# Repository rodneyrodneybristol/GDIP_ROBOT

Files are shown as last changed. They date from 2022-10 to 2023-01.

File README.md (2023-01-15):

# UWE GDIP 2022, GROUP 7D RESISTOR SORTING ROBOT
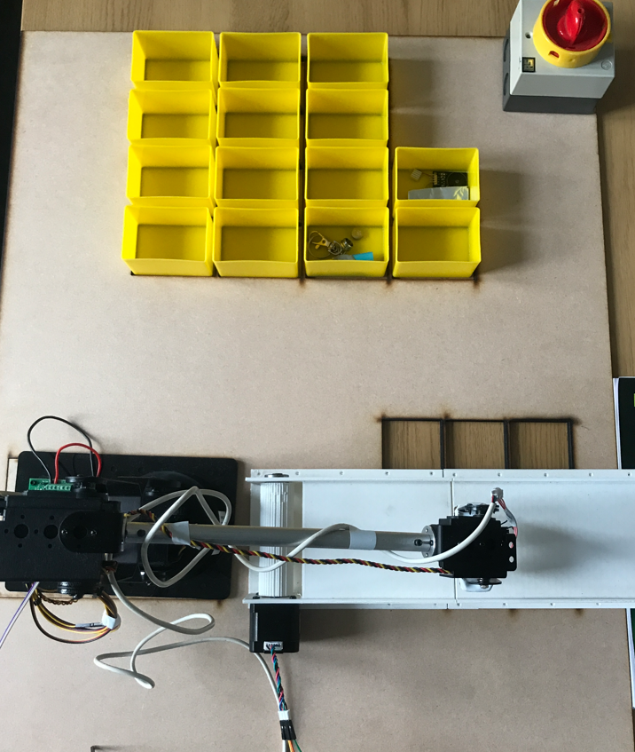
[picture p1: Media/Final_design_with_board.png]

<b>How to assemble and run</b>
<br>
To install:
<br>
```
git clone https://github.com/rodneyrodneybristol/GDIP_ROBOT
```
<br>
or download the .zip repository directly
<br><br>
Install platform IO, to open the firmware files for the motherboard and ohm meter board. 
<br>
Firmware may take a little while to load and build initially if you do not already have the Pi Pico SDK and Arduino frameworks installed. 
<br>
Firmware can be loaded to the Pi Pico directly and the Atmega328p can be programmed using an AVR programmer or Arduino in ISP programmer mode.
<br><br>
to 3D print the conveoyr belt, simply load the provided STLs in to any chopper software. Best to print them vertically to avoid excessive infil.
<br><br>
2 x 5V supplies, with at least 2A each are required  to run this system, one which handles the mobo/servos/ohm meter etc and another for powering the conveoyrs NEMA17 stepper motor. 
<br><br>
Calibration offset for the Robot can be adjusted in the 
```
startAndCalibrateArm();
``` function within the mobo/mainboard main.cpp file. These will need to be set once when loading the system, in case any servos have serious offsets. This allows for more precise movements of the arm.
<br><br>

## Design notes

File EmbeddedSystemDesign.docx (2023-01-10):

AL5D Robot arm project.

SHOULD WE MAKE THE CONTACT PLATE OURSELVES OUT OF COPPER?

# Problems to be solved

- Implement kinematic algorithm to move robot arm to location of resistor to be sorted.
- Read the value of a resistor using the 2 probes on the modified gripper design.
- Turn electromagnet on.
- Based on the returned value, tell the robot arm to sort the resistor into the appropriate container.
- Turn electromagnet off.
- Implement safety features (master stop).
- Implement Calibration features.
- Possibility of datalogging.

# Technical considerations.

Choice of embedded system.

First the documentation for the Lynxmotion ‘SSC-32u’ arm controller board was analysed. The control system uses a UART serial connection to receive control commands and to send some return data back as well. The UART connection could be configured to a desired baud rate and then controlled from any other device with a serial port.

A basic serial message to move all the servos on the robot arm can be sent in the form of a string, beginning with # and ending with a carriage return <cr>

#0P1425#1P1500#2P1500#3P700T2000<cr>

The first part of the command:

#0P1425

#0 means that servo 0 is being controlled, then p1425 sets that servo to that position. So 1P, 2P, 3P is then controlling another servo.

The last command:

T2000

Sets the travel speed in milliseconds, so in this example the motors will allow move to their desired positions in 2 seconds.

The absolute (maximum) control command was measured to be no greater than 34 Bytes, therefore that is the total length of a message in our system and memory allocation considerations going forward were based on that measurement.

To read the value of resistors, the gripper design is based on 2 probes which act like ohm meter probes to read the resistance of the gripper and an electro-magnet which then picks the resistor up for it to be sorted to a predefined location. For reliable measurements, the PCB to read the value must be mounted as close to the probes as possible, as noise and resistance could affect the analogue reading over longer distances.

Due to the reliability of serial communication over the working envelope of the robot arm:

(https://www.digikey.com/en/articles/uarts-ensure-reliable-long-haul-industrial-communications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,485%20or%20RS%2D422%20interfaces.)

“With appropriate line drivers, a UART can work over long distances: from 15 meters (m) for the RS-232 serial data bus to 1000 m for RS-485 or RS-422 interfaces” [22 May 2019]

The proposed design utilises an ohm meter on the arm itself, to read the value of the resistor and increase the reliability of that analogue reading, then send the processed reading to another “master” microcontroller which can then activate the robot arm. This will mean making 2 PCBs, one which could be mounted on the gripper and one to remain at the base acting as a master controller.

Given that the SSC-32u controller used serial messages to control the board, a serial connection would be needed for communication with the gripper and considering that the system may want to have flexibility to communicate with other devices such as a desktop computer alongside the arm controller. A microcontroller

Due to the recent upsets in the global semiconductor supply chain, certain, more popular microcontrollers, such as STM32F103vgt6 (core of the STM “blue pill”) and Atmega328p (core of the “Arduino Nano”) have become increasingly difficult to source, with back order waiting times sometimes over a year. An alternative solution was required here to bypass this issue.

Two contenders for the role in this case were the ESP32 or the RP2040 (Pi Pico/ Pico W). Seeking to keep the costs low and looking to develop further on a relatively new platform, the RP2040 was chosen due to its low cost and wide availability. The Pi Pico W development board was then set up to allow development of the system using breadboards, protoboard and in-house PCBs, made using a PCB router.

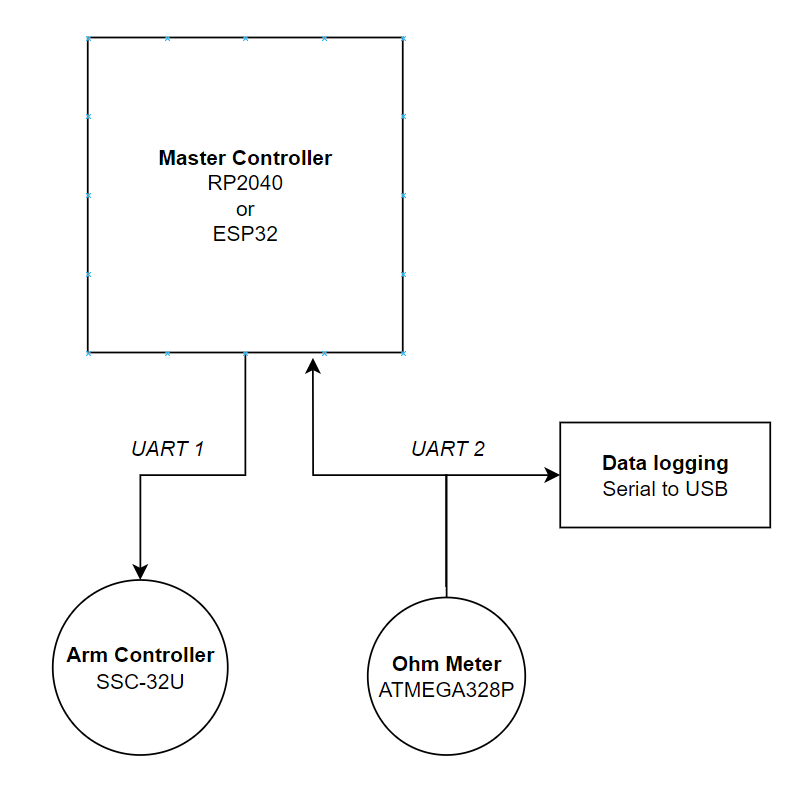
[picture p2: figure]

# Ohm Meter

The project required a system of reading values of resistance into a microprocessor, the value then denoting what box to sort the resistor in to.

Utilising an analogue to digital converter (ADC), resistance could be read from an unknown resistor by creating a voltage divider with that and another resistor of known value. Reading the voltage from that divider will give the resistance.

The resistance of known value is not random and does need to be within a relative range of that which is being tested. Thus, a feature which is seen in most multimeters, an auto ranging feature must be implemented to allow a wide range of values to be read without manually changing the resistor of known value.

The auto ranging design was chosen, using five PNP transistors, acting as switches between different known values of resistance, due to its small layout size compared to some other methods such as using an analogue multiplexer and some peripheral logic.

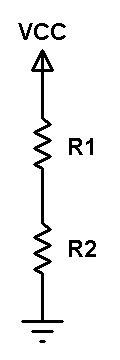
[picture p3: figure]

Applying voltage divider equation to the above circuit we get:
Voltage across resistor R1: VR1 = VCC x R1/(R1 + R2)
Voltage across resistor R2: VR2 = VCC x R2/(R1 + R2)

Assume that the resistance of R1 is known and R2 is unknown, by applying voltage divider equation we can easily get the value of R2 by measuring the voltage across it where: R2 = VR2 x R1/(VCC – VR2). If VR2 is equal to VCC then R2 = infinite.

How to measure R2 voltage (VR2):
The voltage is an analog signal and we can measure it using ADC (Analog-to-Digital) converter which converts analog data into digital data. The Arduino board with ATmega328P microcontroller (UNO, Nano, Mini …) has a built-in 10-bit ADC module where VCC (+5V) is represented by 1023 and 0 volts is represented by 0 (if VDD is already used as positive voltage reference).

Do we need fixed voltage reference?
Actually, I think there’s no need for a fixed voltage reference and adding it will not give a big change in the results. Because the voltage divider positive terminal (VCC) and the ADC positive reference voltage are connected to the same point and any change of this point voltage will affect both the voltage divider output and the ADC module.

Multirange ohmmeter:
To get a good value of the resistor to be measured, a multirange ohmmeter should be used.
The multi-range ohmmeter may also use voltage divider technique with different values of resistor R1. The following image shown a simple diagram of multi-range ohmmeter:

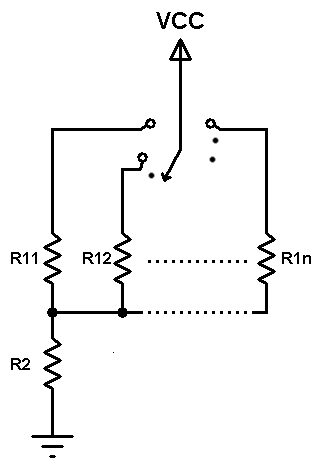
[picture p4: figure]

The multi-range ohmmeter is based on a mechanical switching device with 1 input and multi output. At any time just one known resistor (R11, R12 … R1n) is connected in series with the unknown resistor R2.

Auto-ranging ohmmeter:
The auto-range ohmmeter operates the same as the multi-range ohmmeter except that the mechanical switching device is replaced by electronic switches such as transistors driven by an intelligent device (microprocessor, microcontroller …) that decides which switch is closed according to the resistance value of the unknown resistor.

Project Hardware Required:

- Arduino board
- 5 x PNP transistor (2SA1015 (http://www.unisonic.com.tw/datasheet/2SA1015.pdf), 2N3906 (https://www.onsemi.com/pub/Collateral/2N3906-D.PDF) …)
- 2 x 100nF ceramic capacitor
- 5 x 4.7k ohm resistor
- 2M ohm resisor
- 100k ohm resistor
- 10k ohm resistor
- 1k ohm resistor
- 100 ohm resistor
- 330 ohm resistor
- 10k ohm variable resistor or potentiometer
- Breadboard
- Jumper wires

Arduino autoranging ohmmeter circuit:
Project circuit diagram is shown below.
Note that all the grounded terminals should be connected together.

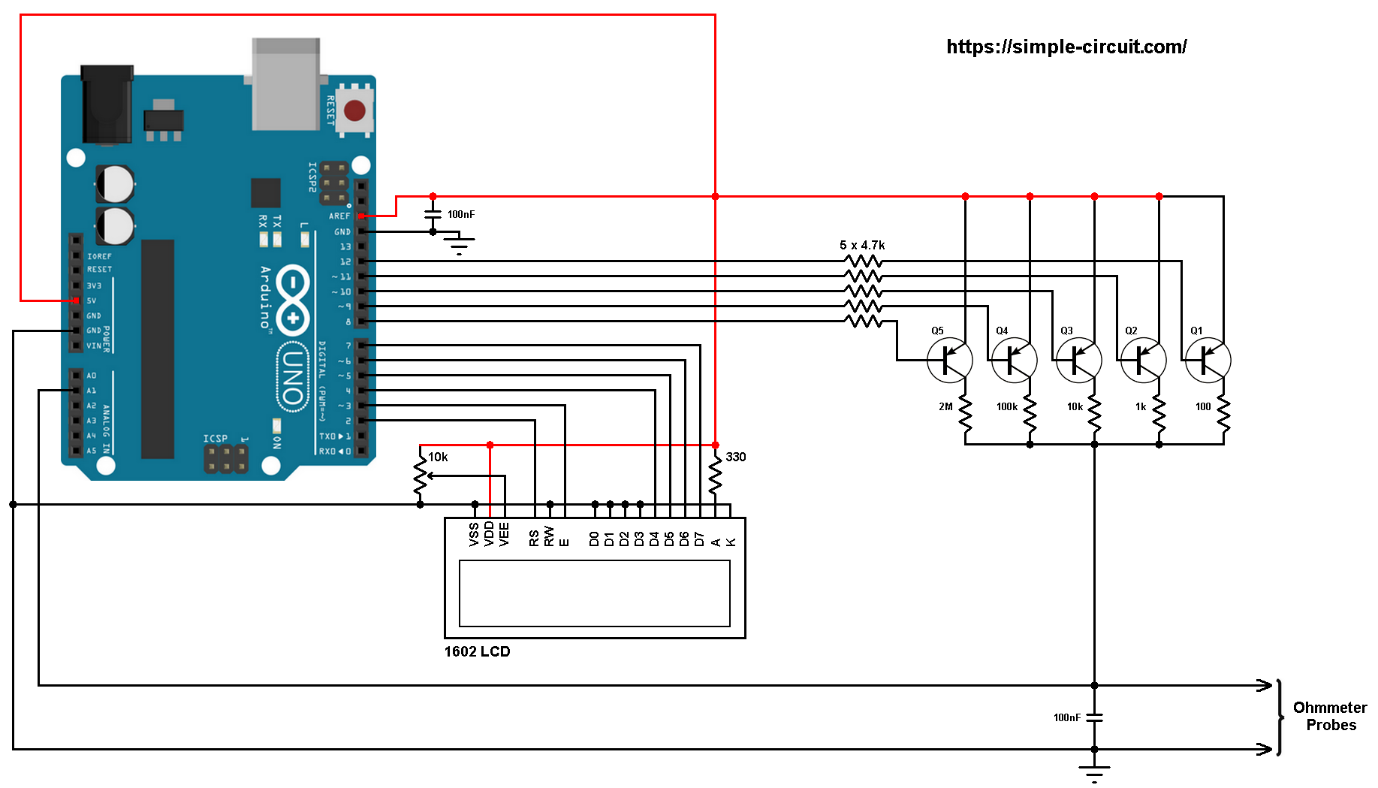
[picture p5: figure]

The resistor which we want to measure is connected between Arduino analog channel 1 (A1) and GND as shown in the above circuit diagram (Ohmmeter Probes). The 100nF capacitor is used to stabilize the voltage across the unknown resistor.

The five PNP transistors Q1 ~ Q5 are general purpose transistors and they are of the same type 2SA1015, 2N3906 or equivalent. They are used as electronic switches for our autoranging ohmmeter.
The emitter terminal of the five transistors are connected together to 5V pin of the Arduino board.

The collector of each transistor is connected to a different resistor. At any time there is only one ON transistor whereas the others are OFF. For better accuracy, each of the 5 resistors should have tolerance of 1% or lower.
Also, each transistor base is connected to Arduino digital pin through 4.7k ohm resistor.

The AREF pin of the Arduino board should be connected to 5V pin with 100nF capacitor between it and GND pin.

MY WORDS:

In the circuit diagram, the resistor being measured is connected between the A1 pin and GND on an Arduino board. A 100nF capacitor is included to steady the voltage across the unknown resistor. The circuit also includes five PNP transistors (Q1-Q5), which are all of the same type (2SA1015, 2N3906 or equivalent) and function as electronic switches for the ohmmeter. The emitters of the five transistors are all connected to the 5V pin on the Arduino board. Each transistor's collector is connected to a different resistor, with only one transistor turned on at a time. For improved accuracy, it is recommended that each of the five resistors has a tolerance of 1% or lower. The base of each transistor is connected to an Arduino digital pin via a 4.7k ohm resistor. Additionally, the AREF pin on the Arduino board should be connected to the 5V pin and have a 100nF capacitor between it and the GND pin.

# Master Controller

Since the master controller will require 2 separate UART connections, one for connecting to the ohm meter and another for connecting to the robot arm unit, using an ATMEGA328p based system would not be sufficient. Either an ESP32 (3 UART) or RP2040 (2 UART) based system would overcome this obstacle, both systems can be programmed using Arduino or Platform IO, as well as “bare metal” using their own respective SDKs.

# Electromagnet

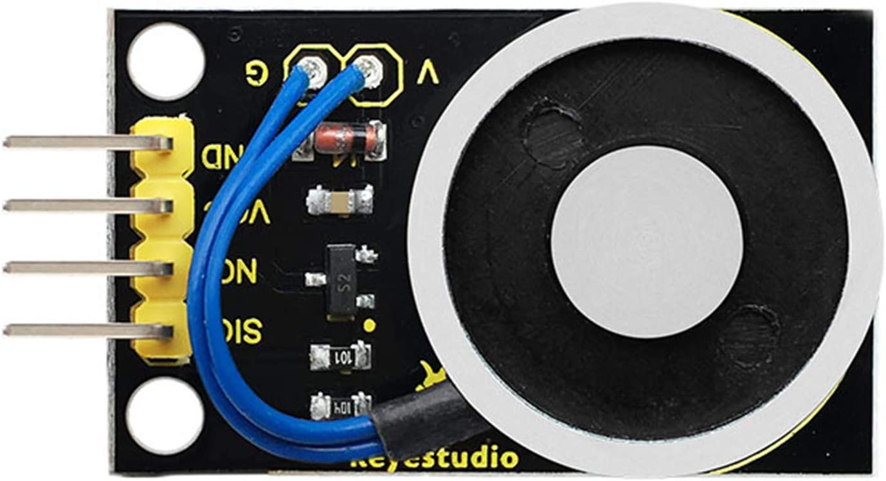
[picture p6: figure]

https://wiki.keyestudio.com/KS0320_Keyestudio_Electromagnet_Module_(Black_and_Environmental-friendly)

- Working Voltage: DC 5V
- Working current: 0.3A (maximum)
- Maximum power: 3W

The above electromagnet can be controlled using a PWM signal on its SIG pin, the larger the PWM value the larger the magnetic field (up to 1kg, this needs to be tested).

V & V

Managing bugs:

50% of microelectronics development is V&V as opposed to design. (lol wayyyy more)

Validation are we building the right system?

Verification ae we building the system right? (correctly?)

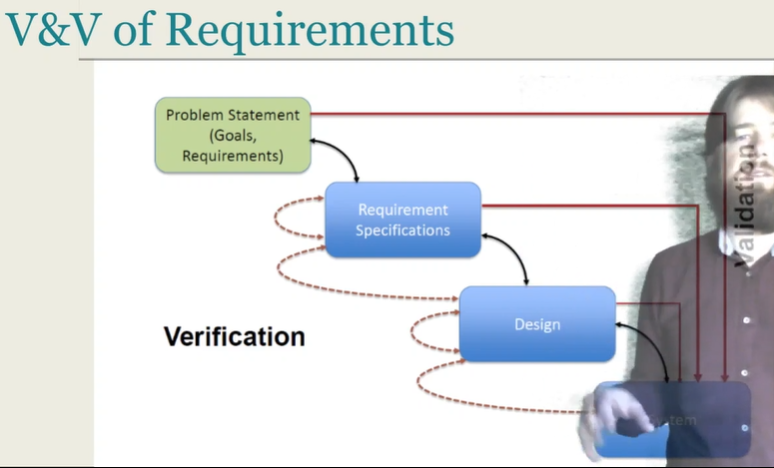
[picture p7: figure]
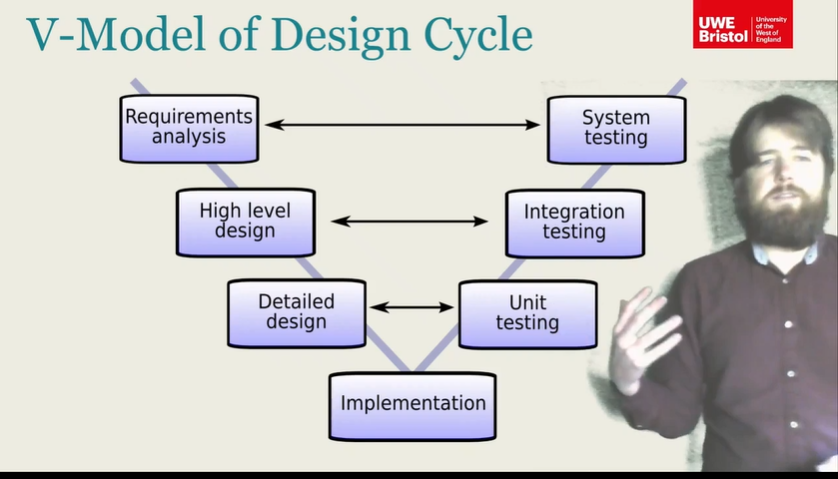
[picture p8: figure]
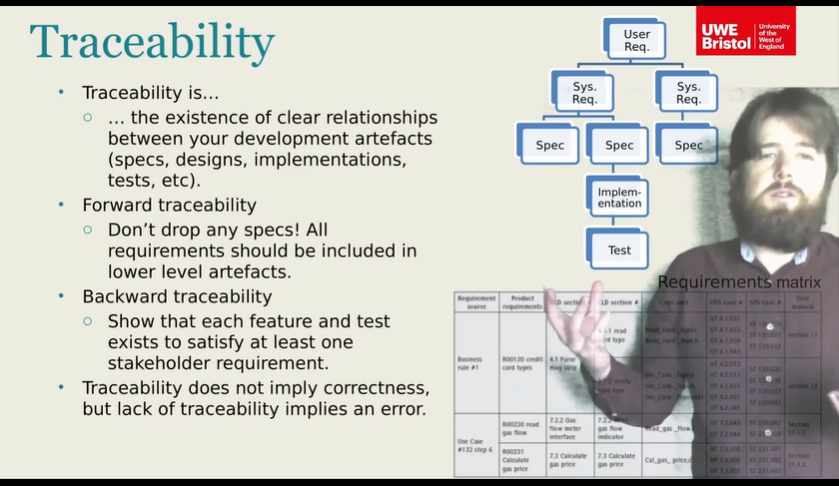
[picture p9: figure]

Requirements matrix

Talk about gripper iterations.

First one was too long, so mounted the PCB at 90 degrees to previous design.

Second design did not have correct mounting holes for the current al5d arm.

Third iteration did not have a solid enough infill and was very weak and broke on the first stress test. Potentially should add some sort of composite analysis here? This can be very basic.

Talk about initial building of system using Atmega328p on Arduino Nano, then upgrading the design to the raspberry pi pico, the pico and the RP2040 being much cheaper and readily available where as the Atmega328p is currently difficult to get hold of. Then finally settling on the Pico W with included WiFi capability to allow for possibility of exploring datalogging using JSON and an Amazon AWS server with get/puts.

Talk about the iterations of the base design and the justification for that in terms of allowing the system to be built by anyone using the cloned github repository.

Code snippets and pseudo code to justify the mathematical kinematic model.

Notes make 2nd gantt chart

PCB designs.

Take pictures of stuff

Summaries

What could we do better? Add datalogging and wifi control, better conveyor system. Have our own motor control board so as not to use the SCC-32u

Each row in this array is in the order, (x, y, resistance in ohms), and can be configured to any value between 100R to 2M

long BoxCoordinatesXY[10][3] = {

// Row 1

{0, 260, 1000}, //1k

{0, 330, 4700}, //4.7k

{0, 390, 10000}, //10k

// Row 2

{80, 270, 20000}, //20k

{80, 330, 47000}, //47k

{80, 390, 86000}, //86k

// Row 3

{160, 270, 100000}, //100k

{160, 330, 180000}, //180k

// Row 4

{240, 270, 470000}, //470k

{240, 330, 1000000}}; //1M

Calibration function

void startAndCalibrateArm()

{

Serial.println("#0P1425#1P1500#2P1500#3P700T2000\r"); // starting position

Serial.println("#2PO-100\r"); // calibrate

// DEBUG

delay(2000);

}

Kinematics string function
char *getArmCode(float x, float y, float z)

{

float grip_angle_d = 68;

// grip angle in radians for use in calculations

float grip_angle_r = radians(grip_angle_d);

// Adjustment so that the gripper hits the floor at z=0;

z += 70;

// Base angle and radial distance from x,y coordinates

// float d = sqrt( x*x + y*y ); //distance from base center to x,y coordinates

float phi = 90.00;

float bas_angle_r = atan2(x, y);

float L = sqrt((x * x) + (y * y));

// L is y coordinate for the arm

L -= cos(phi) * GRIPPER;

y = L;

// Grip offsets calculated based on grip angle

float grip_off_z = (sin(grip_angle_r)) * GRIPPER;

float grip_off_y = (cos(grip_angle_r)) * GRIPPER;

// Wrist position

float wrist_z = (z - grip_off_z) - BASE_HGT;

wrist_z -= sin(phi) * GRIPPER;

float wrist_y = y - grip_off_y;

// Shoulder to wrist distance ( AKA sw )

float s_w = (wrist_z * wrist_z) + (wrist_y * wrist_y);

float s_w_sqrt = sqrt(s_w);

// s_w angle to ground

// float a1 = atan2( wrist_y, wrist_z );

float a1 = atan2(wrist_z, wrist_y);

// s_w angle to SHOULDER

float a2 = acos(((sh_sq - el_sq) + s_w) / (2 * SHOULDER * s_w_sqrt));

// shoulder angle

float shl_angle_r = a1 + a2;

float shl_angle_d = degrees(shl_angle_r);

// elbow angle

float elb_angle_r = acos((sh_sq + el_sq - s_w) / (2 * SHOULDER * ELBOW));

float elb_angle_d = degrees(elb_angle_r);

float elb_angle_dn = -(180.0 - elb_angle_d);

// wrist angle

float wri_angle_d = (grip_angle_d - elb_angle_dn) - shl_angle_d;

// Servo pulses

float bas_servopulse = 1500.0 - ((degrees(bas_angle_r)) * 11.11);

float shl_servopulse = 1500.0 + ((shl_angle_d - 90.0) * 6.6);

float elb_servopulse = 1500.0 - ((elb_angle_d - 90.0) * 6.6);

float wri_servopulse = 1500 - (wri_angle_d * 11.1);

// Set servo pulses

// create string for output

// Added some offsets here, not sure if they are correct, they seem to work though

sprintf(output, "#0P%ld#1P%ld#2P%ld#3P%ldT2000\r", ftl(1500 - bas_servopulse + 500), ftl(shl_servopulse), ftl(elb_servopulse), ftl(wri_servopulse + 400));

return output;

}

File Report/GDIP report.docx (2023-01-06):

# Resistor sorting robotic arm

We could have an image of our arm here maybe?

Name | Student ID
Dominic Pennycook | 19006106
John Nicola | 19007312
Saad Khan | 20010279

Insert a table of figures after content – in the references tab under captions

Abbreviation | Meaning
RSA | Resistor Sorting Arm
V&V | Verification and Validation
MVP | Minimum Viable Product
V&V | Verification and Validation
RMP | Risk mitigation plan

# Introduction

## Purpose of the report

Due to the complex nature of the project and the high level of interest from stakeholders this report was created showing the process’s taken to ensure the products feasibility and suitability to the problem proposed and the project scope laid out later. Each section will aid in the completion of future project as well as show the suitable steps in an engineering projects lifecycle were completed to a high level. Important parts of the project management are included and the last key section of the report allows a deeper dive into what could be improved for future projects and what lessons were learnt.

## Scope of the project

The resistor sorting arm (RSA) needed to quickly and accurately sort through a group of resistors with minimal human assistance. The arm needed to measure resistor resistance in a set location, pick the resistor up and move it to the correct box. While our MVP works with the E12 resistor series modifications too the code would allow an easy change to a different set of resistors and with more altering additional boxed could be added allowing more different resistors too be sorted.

## All necessary documentation

GitHub was used extensively throughout the project allowing all pertinent documentation to be stored in one location. Use of software similar to GitHub allows excellent version control and advanced team collaboration and allowing individuals to produce documentation at their own rate. The link to this projects GitHub repository is XXX, and the can be found in the uploaded documentation on blackboard. The necessary password is XXX

# Project management

## Risks and Management

From the onset of the project risks were being assessed and added to the risk mitigation plan. Initially a comprehensive list of all related risks was created and then added to through the project, each team member regularly reviewed the plan and made sure it was still suitable. The risk was categorised using Figure XX & XX2, then using conditional formatting in excel it was it was simple to understand which risks were most dangerous to the project. Each of the initial risks were use in creating the Gantt chart and allowing additional time to events which had a higher likely hood of being delayed.

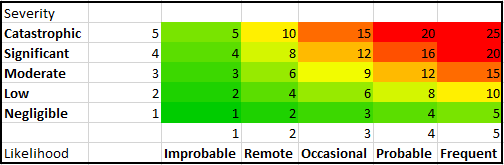
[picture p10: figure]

Figure 1 - Risk Characterisation Table

Figure 2 - Risk Key

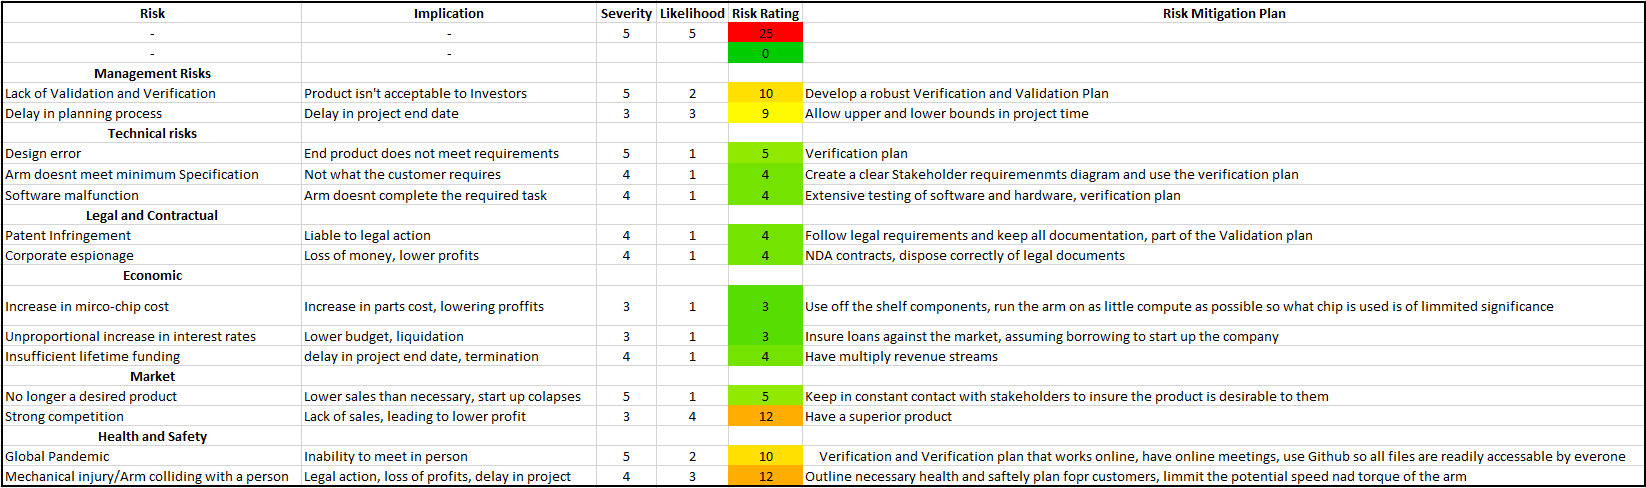
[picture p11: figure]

Figure 3 - Risk's and Mitigation Plans

The Verification and Validation (V&V) plan (covered later in this report) was vital to the success of the project. V&V allowed the confirmation that all sections accomplished were traceable to the system and high-level design, and also completed their intended outcome, without adding bloat to the project. As V&V was so vital to the project the robust plan was formed early on and rigidly maintained throughout the venture.

The Design risks heavily rely on a vigorous V&V plan, through this the likelihood of a project delaying/cancellation issue is extremely unlikely. This is further evidence of the need for a competent V&V plan. Legal and contractual issues would be a greater issue past this project’s scope and after the production of the minimum viable product (MVP) but designing the arm from scratch will minimise these issues. Economic issues are largely out of the control of the start-up, however suitable mitigation in the case of an issue is still needed and provided. Through continued discussion with the stakeholders, described in the High-level design section, there is an undersaturated market for this product and minimal competition. However, if the market decreased/becomes oversaturated this could financially cripple the company so continued talks are necessary. As with any product, a suitable look into health and safety in the manufacture and use of the product is necessary and the necessary documentation will be provided for both.

The RMP was regularly updated periodically in conjunction with the project and GitHub as used for version control ensuring all different stages of the plan were saved and could be accessed if needed. As the RMP was created originally at the beginning of the project all team members knew what the risks were and how to avoid them happening allowing the project to complete smoothly with minimal issues.

## Team allocation

At the start of any project, it is vital to determine and define the team structure and roles, making sure everyone in the team understands their responsibility and roles. This breakdown is detailed in Figure XX 4). To further emphasise each team members roles and responsibility a responsibility matrix was created (Figure XX 5). This level of planning allowed team members to know what they needed to complete and who had the information to help them, also allowing individual members to make sure everyone else had completed their section.

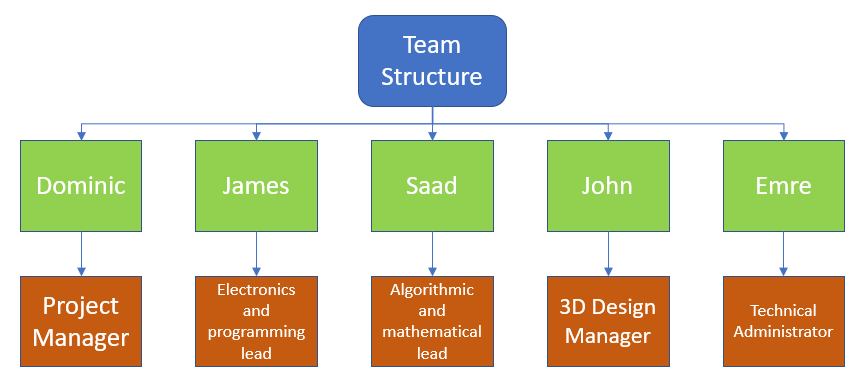
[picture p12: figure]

Figure 4 – Team structure

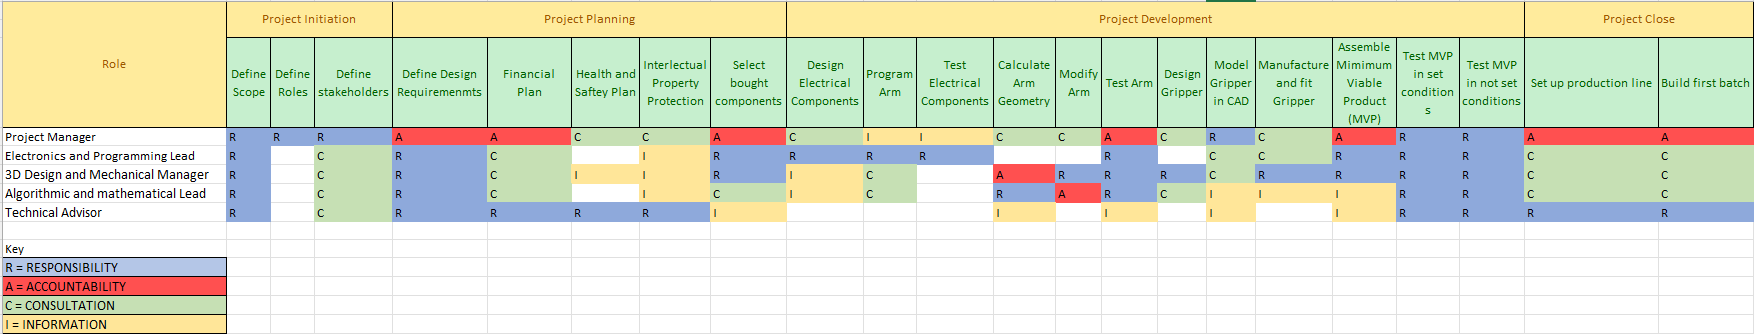
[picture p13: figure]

Figure 5 - Responsibility matrix

## Planning and Scheduling

- Planning and scheduling

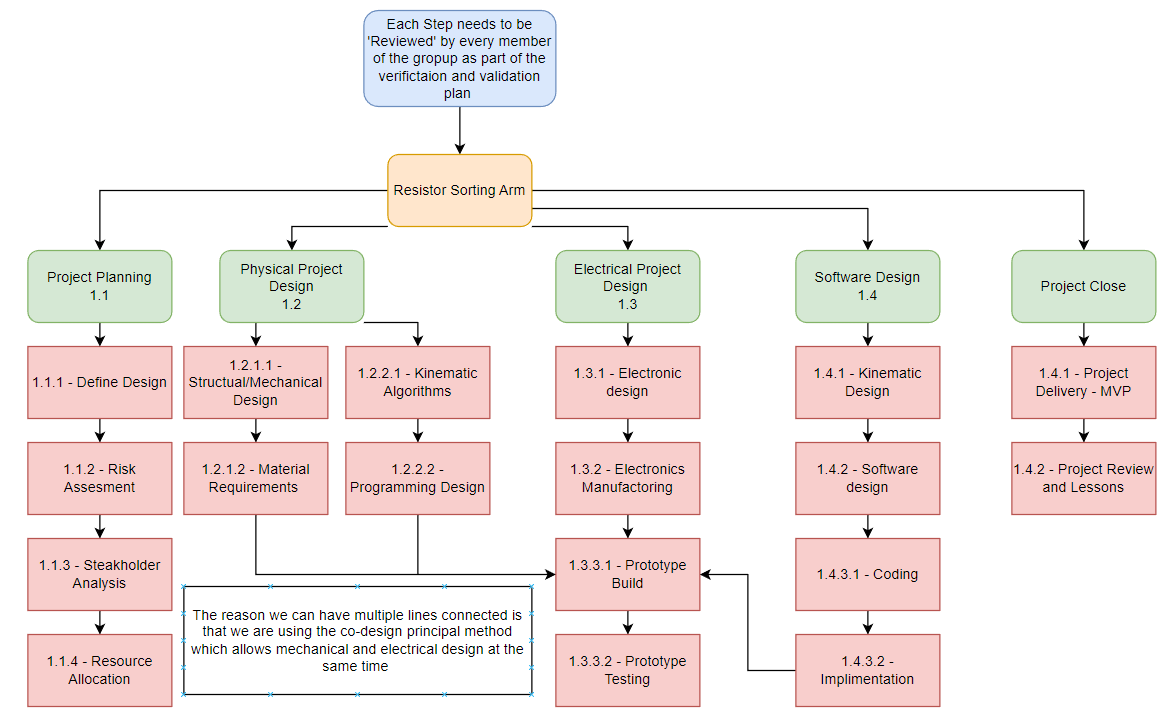
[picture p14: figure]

Figure 6 - Work Breakdown Structure

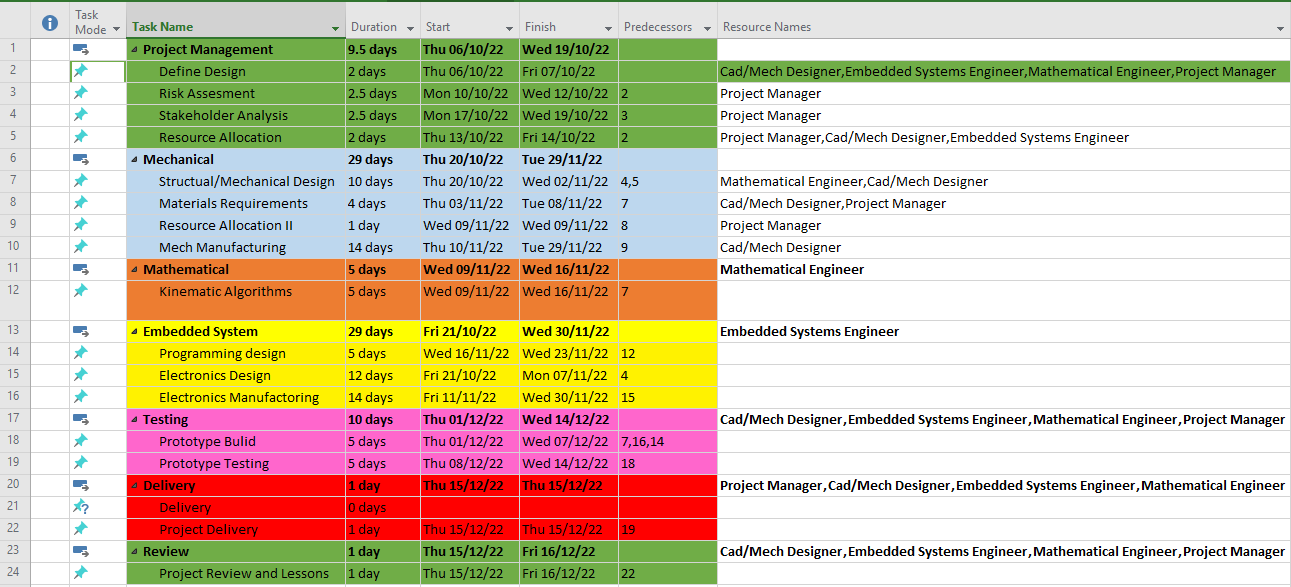
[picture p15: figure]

Figure 7 - Project Gant Chart 1

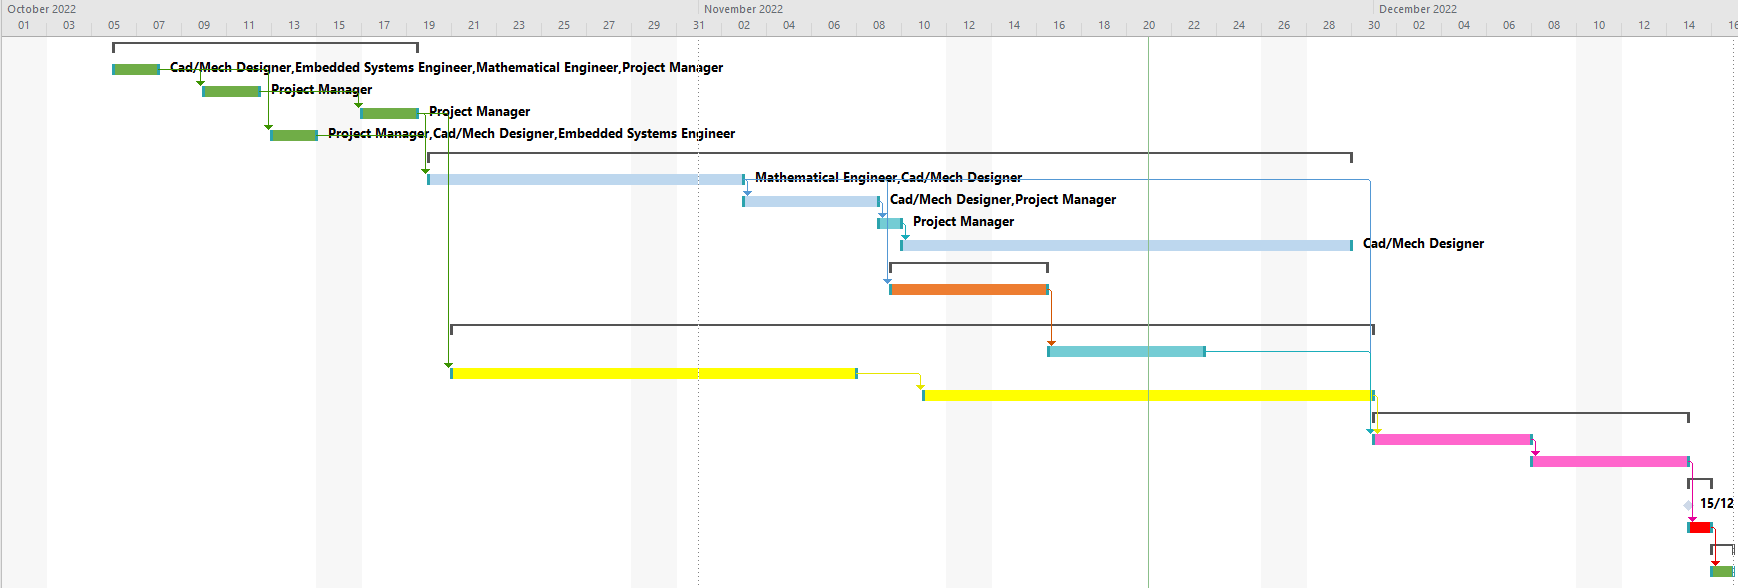
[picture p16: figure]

Figure 8 - Project Gant Chart 2

## Progress monitoring and Coordination

During the project weekly meetings were held and comprehensive meeting minutes were taken, as seen in the GitHub repository. This allowed everyone to know what had been discussed and also what they need to complete in order to stay on track and complete the project in time. Any task that was not completed for any reason was moved too the next weeks minutes and the project manager followed up with help to make sure they were completed. This use of meeting minutes on GitHub gave clear instructions to every team member on what was necessary to be completed, when uploaded to GitHub the meeting minutes document was available to everyone and any changed that were made would be visible.

# High-level design

## Top-Level System Design

- Presentation of top-level system design. Clear presentation of top-level system design. Clear presentation of high-level design of the main subsystems (e.g. software, electronics). High level designs address all requirements appropriately.

Top level system design and high-level design require conversation with the stakeholders, to ensure all stakeholders are considered each team member had a template stakeholder analysis which allowed multiple stakeholders and their importance along with other metrics which decided their allocation in the stakeholder management document. With each team member independently conceiving a stakeholder analysis the likelihood of a potential stakeholder being missed is drastically reduced allowing a more exhaustive management of the stakeholders. All members included the electronics technical help team at the University of the West of England as a key stakeholder providing the unique possibility to have their opinion every week during the meetings held. This close management of a key stakeholder allowed the project to stay on track and gave very good system and high level design criteria.

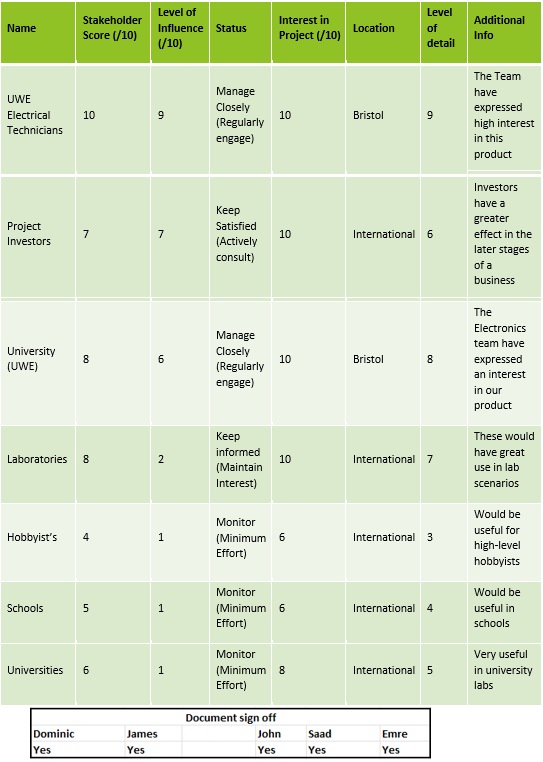
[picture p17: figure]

Figure 9 - Stakeholder Analysis

Utilising the stakeholder analysis and either talking directly to the stakeholder or using our tutor as that stakeholder a list of all the requirements (Figure XX) was created and the stakeholder sign off was used. This requirements list document allowed a clear view of what was desired by the clients and what we needed to do to complete the project to satisfaction. Once the stakeholders, the UWE Fet Team and a representative group of hobbyists, had read the requirements list any changes were made and the document was signed off.

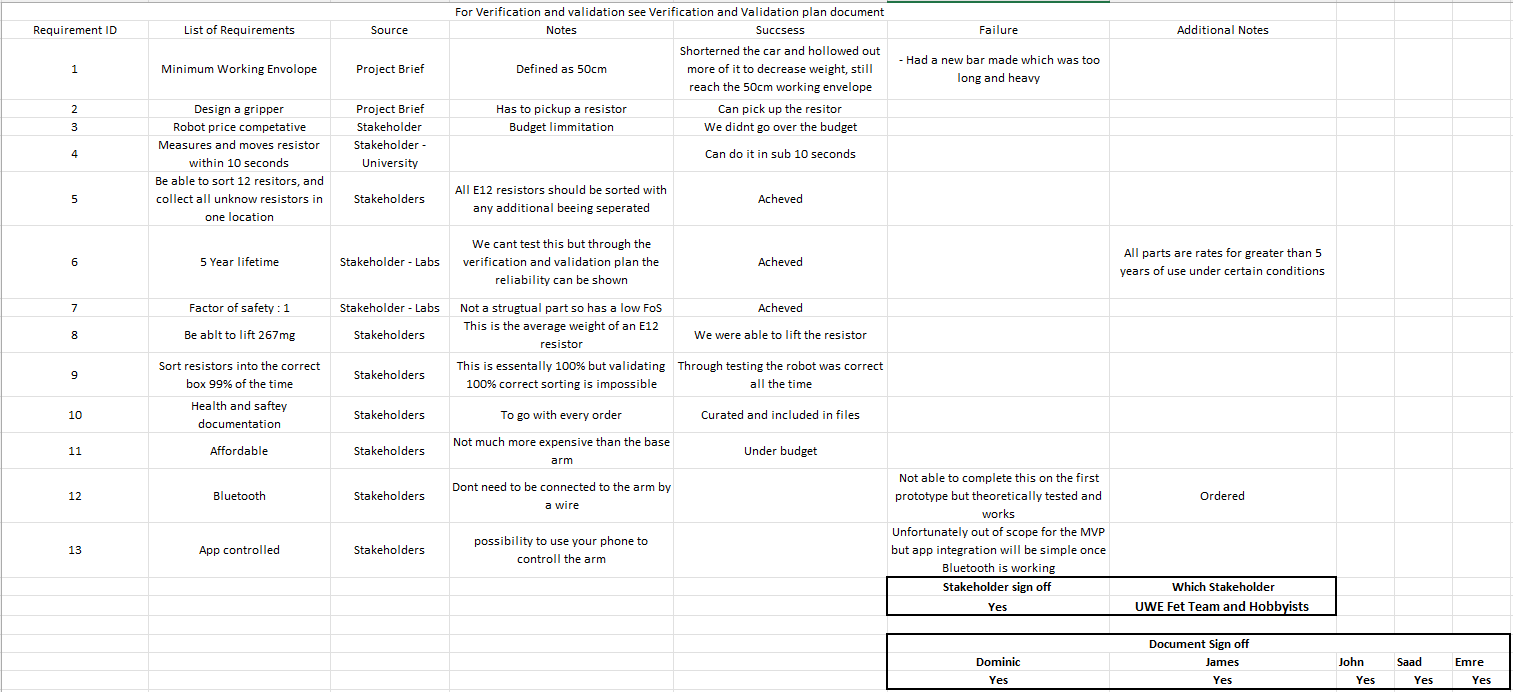
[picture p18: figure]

Figure 10 - Requirements list

## High-Level Mechanical Design

- Presentation of high-level design of the main subsystems (e.g. software, electronics).

## High-Level Software Design

- Presentation of high-level design of the main subsystems (e.g. software, electronics).

## High-Level Electrical Design

- Presentation of high-level design of the main subsystems (e.g. software, electronics).

## Requirement Analysis

'- Requirements analysis

## Traceability

The High Level design requirements were specified from user requirements, as is corroborated by the Requirements list. This list was form in collaboration with various stakeholders to produce a comprehensive idea of what the robot was required to complete. Each high-level design has a direct link to s system level design validating that the stakeholders would want it.

# Financial, Regulatory and Intellectual Property considerations

# Low-Level Design

## Implementation

'- Lower-level specifications and implementations to address the requirements.

- description of the process for developing and implementing the low-level designs, including justification of key decisions.

Things to include: create specifications that each design must fulfil, and mark against design

Justification of the base – why we created a base/ its purpose - mechanical

Why we created an electromagnetic gripper, process of coming to that conclusion, difficulties with a mechanical based gripper - mechanical

How the gripper works - electrical

Reason for having a treadmill/ something to put resistors on (idk what its actually called) - mechanical

How we measured the resistance/ why we did it this way? - electrical

Explanation of kinematics code – software

Maybe should also include some stuff on the programming?

Have a sequence diagram of how the outside world interacts with our robot and how it interacts with the world

- Will look into this

## Low-Level Documentation

- Clear and accessible documentation of low-level designs.

Gripper, base design, maybe some electromagnet stuff

## Traceability

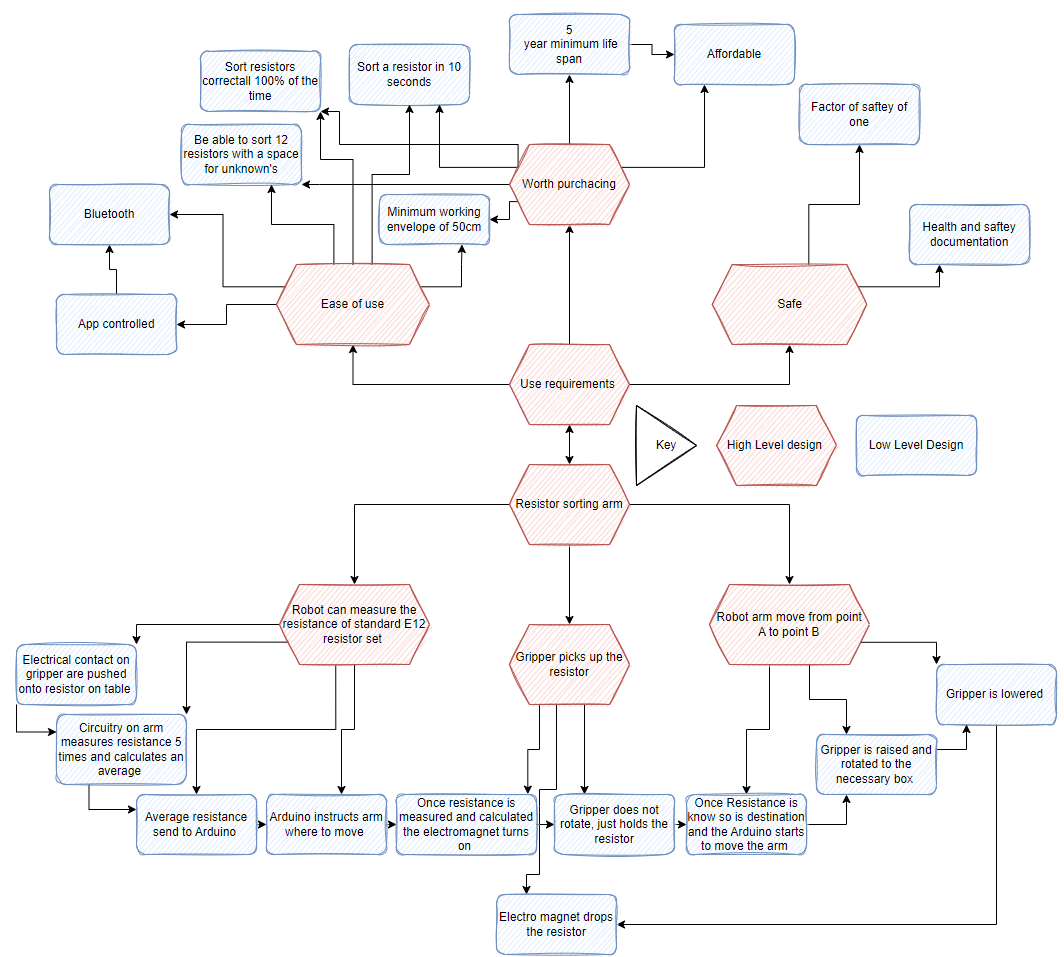
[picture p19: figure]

Figure 11 - High -> Low level design with traceability

# Verification and Validation (V&V)

## V&V Plan

The V&V plan ensures that the end product is designed and built well and what the customer desired. To accomplish this a competent V&V plan was created at the onset of the project and strictly adhered to, this relied heavily on the V&V matrix (Figure XX) and the individual sign off.

A V&V matrix (Figure XX) allows for every key aspect of the project to be officially tested and verified to both work, and contribute to what is desired by the stakeholders. Each of the high-level designs and the lead team member(s) are listed with the ID of the verification used and whether this provided full of partial coverage. The different verifications used are found on the next sheet (Figure XX) and these describe the actions taken and are referenced using ID tags for ease of use. The V&V plan was used throughout the project and shows how successful the project was.

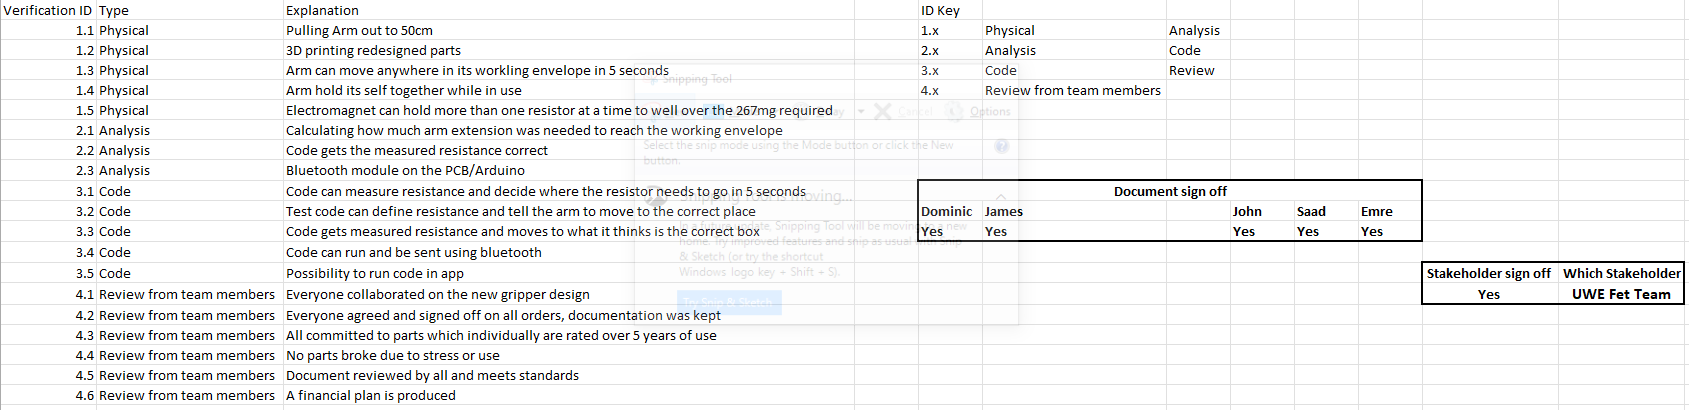
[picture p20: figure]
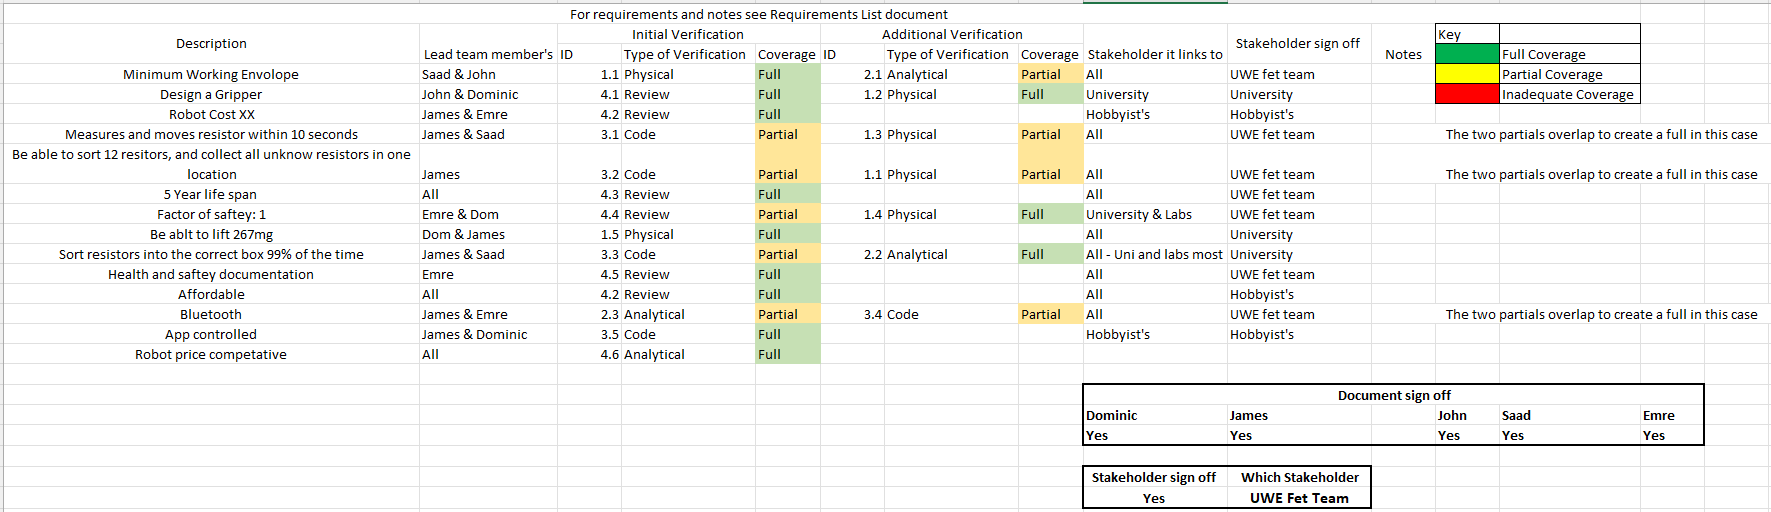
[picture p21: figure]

Figure 12 - V&V Matrix

Figure 13 - Verification Methods

At the end of each project management document a box is displayed which has a location for each member of the team to sign indicating they have reviewed the document and agreed that it is up to standard. Figure XX shows the document sign off box, it is a clear indication that the document has been reviewed and quality checked. In addition to the team member sign off certain documents have a stakeholder sign off which shows a stakeholder has checked the document and that it reaches the standards that are expected (Figure XX). These two boxes verify that what they represent is verified to what is wanted from the customer and also that it is a good solution to the problem.

Figure 14 - Document sign off box

Figure 15 - Stakeholder sign off

## Evidence

Both the Document sign off’s and the V&V matrix provide evidence that the whole of the project has been quality checked and meets the standards of both the team and the stakeholders.

# Reflection and Evaluation

## Strengths of our project

- Thoughtful and accurate assessment of strengths and weaknesses in your group's design process.

## Weaknesses of our project

- Thoughtful and accurate assessment of strengths and weaknesses in your group's design process.

## Next steps in our start-up

What we would do to make the product more viable

- Identification of key lessons in generalised terms that can be applied to future projects.

## What we would do differently next time

- Identification of key lessons in generalised terms that can be applied to future projects.

For future projects a more indepth review into what the customer wants as well as a larger V&Vplan would be beneficial.

Group Design and Integration Project – UFMFV8-15-3 - Group 7D

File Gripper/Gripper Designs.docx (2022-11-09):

1

https://www.amazon.co.uk/ANCIRS-Stainless-Electronic-Components-Accessory/dp/B08FHXDBLG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

Prongs to detect resistance of resistors while on the arm. Pulling motion to open and close gripper.

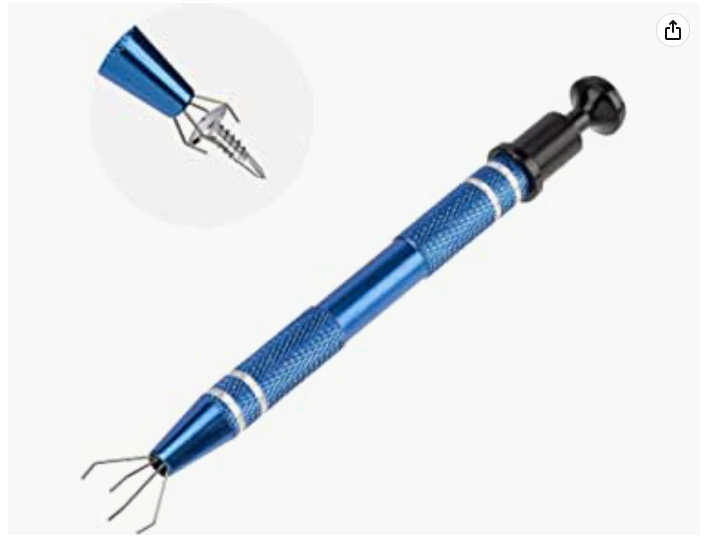
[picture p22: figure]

2

https://uk.rs-online.com/web/p/power-motor-robotics-development-tools/1743254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

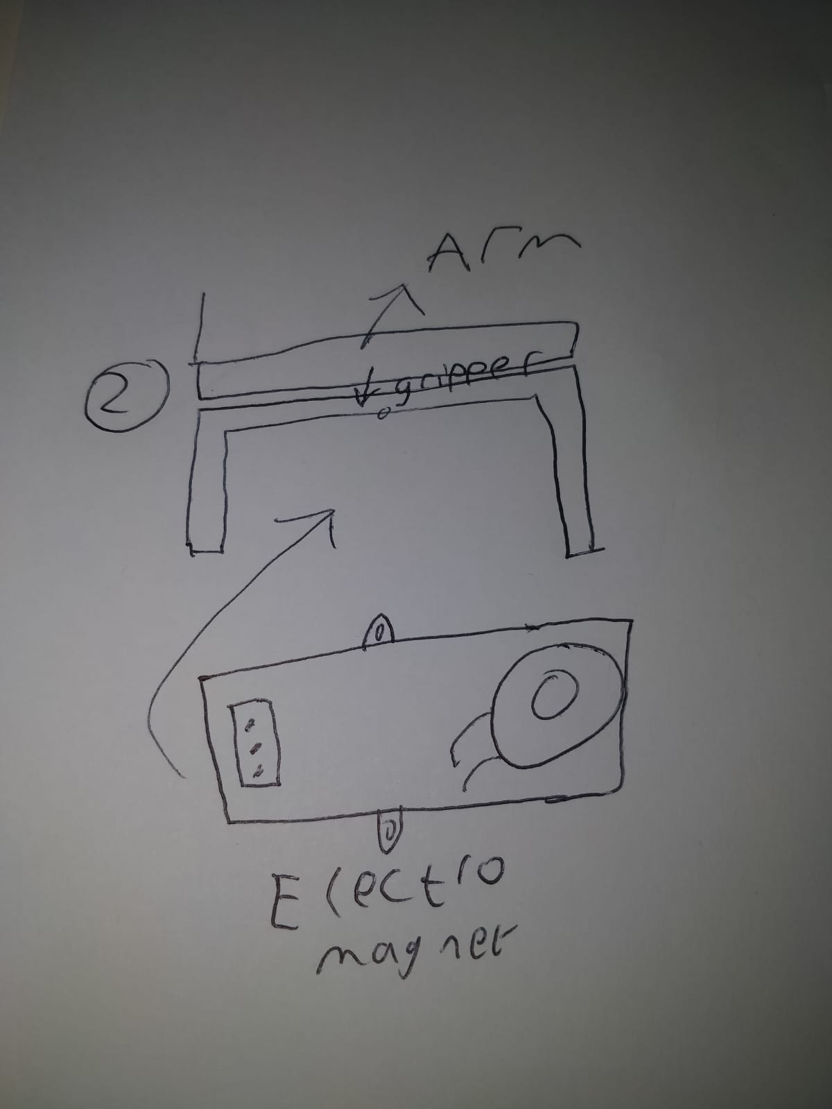
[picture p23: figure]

Electromagnet gripper. Mount Module on the gripper part of the arm.

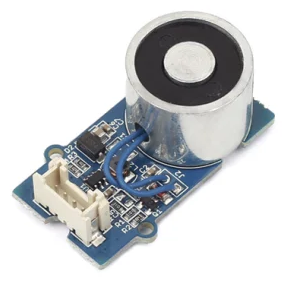
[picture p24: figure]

3

https://uk.rs-online.com/web/p/pick-up-tools/2222160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

Modification of an existing vacuum based pickup tool (similar to that found in a pick and place machine) mounted on gripper, as a way of picking up components, probably more useful for SMD parts.

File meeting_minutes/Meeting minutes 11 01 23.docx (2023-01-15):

In attendance:

John

Saad

Dom

Missing:

James

Emre

What we did

Went through report and mark scheme to assess the report

Ensures every point was covered

What we need to do:

John - talk about base in high level design, move gripper stuff and extension stuff to low level, move old gripper design up to lower level and describe why they were changed and how they have been imporved

Saad – add info about the yellow boxes into low level

All – work on final section – Mainly Saad and John

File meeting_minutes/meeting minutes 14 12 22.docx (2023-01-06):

In Attendance:

Dominic

John

Saad

Absent:

James

Emre

Discussed

Picked up the laser cut board which was wrong and will be re cut

High- and low-level design

Planned writing of report

What everyone needs to do over the Christmas:

Pick up the new laser cutting

Dom – Work on report, Decide who’s doing each section of report

James – Work on report, build prototype

John – Work on report

Saad – Work on report

Emre – Work on report

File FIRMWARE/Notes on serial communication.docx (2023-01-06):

# Notes on serial communication

# Initial code

Single character or number (0to9) = 2 Bytes

For (maximum) control command = 34 Bytes

char output[50] = "";

void serialEvent() {

while (Serial.available()){

// read the incoming byte:

bool newLine = false;

char inChar = (char)Serial.read();

// add it to the output string:

output[strlen(output)] = inChar;

// if the incoming character is a newline, set a flag

// so the main loop can do something about it:

if (inChar == '\r') {

newLine = true;

}

// if we got a newline, print the output string:

if (newLine) {

Serial.print("I received: ");

Serial.println(output);

// print how many bytes

Serial.print("Number of bytes: ");

Serial.println(strlen(output));

// Print how many bytes

// clear the string for new input:

// clear the string for new input:

memset(output, '\0', sizeof(output));

}

}

}

void setup() {

Serial.begin(9600);

}

void loop() {

while(1){

serialEvent();

}

}

# Breakdown of device communication

For communication:

- OhmMeter/Mag Board – Atmega328p
- Main Board- Atmega328p
- SSC-32u – Atmega328p
- Desktop PC Serial port

Communication protocol:

Setup:

- Main board INIT position commands >> SSC-32u

Looping:

- Main Board Move to starting position command >> SSC-32u
- Main board pick up/test position command >> SSC-32u
- Main board TEST ohm command >> OhmMeter/Mag Board
- OhmMeter/Mag Board Send AvgValue >> Main Board
- Main Board MagnetOn command >> OhmMeter/Mag Board
- Main Board Move to box position command, based on AvgValue >> SSC-32u
- Main Board MagnetOff command >> OhmMeter/Mag Board

Settings:

Setting 1:

- Main board send data log >> Desktop PC Serial port

Setting 2:

- Desktop PC Serial port send box assignments >> Main board

Setting 3:

- Main board Read ohm meter (for testing) >> OhmMeter/Mag Board
- OhmMeter/Mag Board Return ohm reading (for testing) >> Main board

Setting 4:

- Main board Turn magnet on (for testing) >> OhmMeter/Mag Board
- Main board Turn magnet Off (for testing) >> OhmMeter/Mag Board

# Breakdown of specific commands:

Position commands:

- INIT position command

Moves the arm to the starting position using the predefined command string:

#0P1425#1P1500#2P1500#3P700T2000

Immediately followed by base (servo 0) offset calibration (other calibration commands can be added too)

#2PO-100

- Move to starting position command

Moves the arm to the starting position using the predefined command string:

#0P1425#1P1500#2P1500#3P700T2000

- pick up/test position command

Moves the arm to the starting position using the predefined command string:

#0P1425#1P1500#2P1500#3P700T2000

Moves down to read resistor using predefined command string:

#0P1425#1P1243#2P1616#3P940T1000

Moves the arm back to the starting position using the predefined command string:

#0P1425#1P1500#2P1500#3P700T2000

- Move to box position command, based on AvgValue

Moves arm from starting position to the desired box. A command for each motor will be combined into a single string followed by a carriage return. This will allow all movements to execute at once.

Values will be generated from X, Y coordinates using the most recently received “AvgValue and the “getArmCode” function.

Magnet commands:

- MagnetOn command

Is simply a string ‘MAG1’;

- MagnetOff command

Is simply a string ‘MAG1’;

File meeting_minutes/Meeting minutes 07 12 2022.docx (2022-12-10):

In Attendance:

Dominic

John

James

Saad

Absent:

Emre

Discussed

Stakeholder management

Parts collection

Waiting for parts

Writing the report

Implementation of kinematics into code

What everyone needs to do:

All – Continue writing the report

Dominic – Add Robot price to requirements list

James – Unit test the code and get a reasonable coverage, Implementation of kinematics into code with Saad

John

Saad - Implementation of kinematics into code with James

Emre

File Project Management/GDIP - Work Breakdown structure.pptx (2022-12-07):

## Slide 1

Resistor Sorting Arm
Project Planning
Project Development
Project Close
Define design Requirements
Electrical Components
Design Electrical components
Test Electrical components
Set up production line
Build 1st off Batch
Arm Design
Calculate Arm Geometry
Modify arm to fit Design spec
Gripper design
Design Gripper
Model gripper in CAD
Produce and Fit Gripper
Select bought in components
Project Initiation
Defining Roles
Defining Stakeholders
Define Scope
Minimum Viable Product
Assemble MVP
Test MVP – In set conditions
Test MVP in not set conditions
Program Arm
Test Arm Geometry
Through out each step each member will review the work being done and sign off that it is of a good standard as part of the validation and Verification of the project
Financial Plan
Health and Safety Plan
Intellectual Property Protection

1.0

1.1

1.2

1.3

1.0.1

1.1.1.1

1.1.2.1

1.2.1

1.2.2

1.2.3

1.2.4

1.3.1

1.0.2

1.1.1.2

1.2.1.1

1.2.2.1

1.2.3.1

1.2.4.1

1.3.2

1.0.3

1.1.2.2

1.2.1.2

1.2.2.2

1.2.3.2

1.2.4.2

1.1.2.3

1.2.1.3

1.2.2.3

1.2.3.3

1.2.4.3

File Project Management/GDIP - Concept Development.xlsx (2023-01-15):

All scores 1 -10, 10 being good apart from Cost - smaller is better
Name: | Dominic | Design Number
Criteria | Impact/1 | 1 |  | 2 |  | 3 |  | 4 |  | 5 |  | 6 |  | Designs | 1 |  |  | The gripper scoops up the resistor and places it on a circuit to measure the resistance |  | 3 | Similar to a claw the resistor is picked up and placed on a circuit to me measured then moved again
 |  | Score | Adjusted | Score | Adjusted | Score | Adjusted | Score | Adjusted | Score | Adjusted | Score | Adjusted
Maintance | 1 | 10 | 10 | 8 | 8 | 6 | 6 | 9 | 9 | 10 | 10 | 5 | 5
Manufactroing | 0.8 | 10 | 8 | 10 | 8 | 6 | 4.8 | 7 | 5.6 | 10 | 7 | 5 | 4
Measuring Ability | 1 | 5 | 5 | 7 | 7 | 5 | 5 | 10 | 10 | 5 | 5 | 7 | 7
Material/Cost | -0.9 | 5 | -4.5 | 4 | -3.6 | 5 | -4.5 | 2 | -1.8 | 6 | -5.4 | 3 | -2.7
Durability | 1 | 10 | 10 | 10 | 10 | 3 | 3 | 10 | 10 | 10 | 10 | 2 | 2
Installation | 0.7 | 10 | 7 | 7 | 4.9 | 6 | 4.2 | 8 | 5.6 | 10 | 7 | 5 | 3.5
Reliability | 1 | 8 | 8 | 8 | 8 | 4 | 4 | 9 | 9 | 8 | 8 | 4 | 4 |  |  |  |  |  |  | 4
 |  | Design 1 total | 43.5 | Design 2 total | 42.3 | Design 3 total | 22.5 | Design 4 total | 47.4 | Design 5 total | 41.6 | Design 6 total | 22.8
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

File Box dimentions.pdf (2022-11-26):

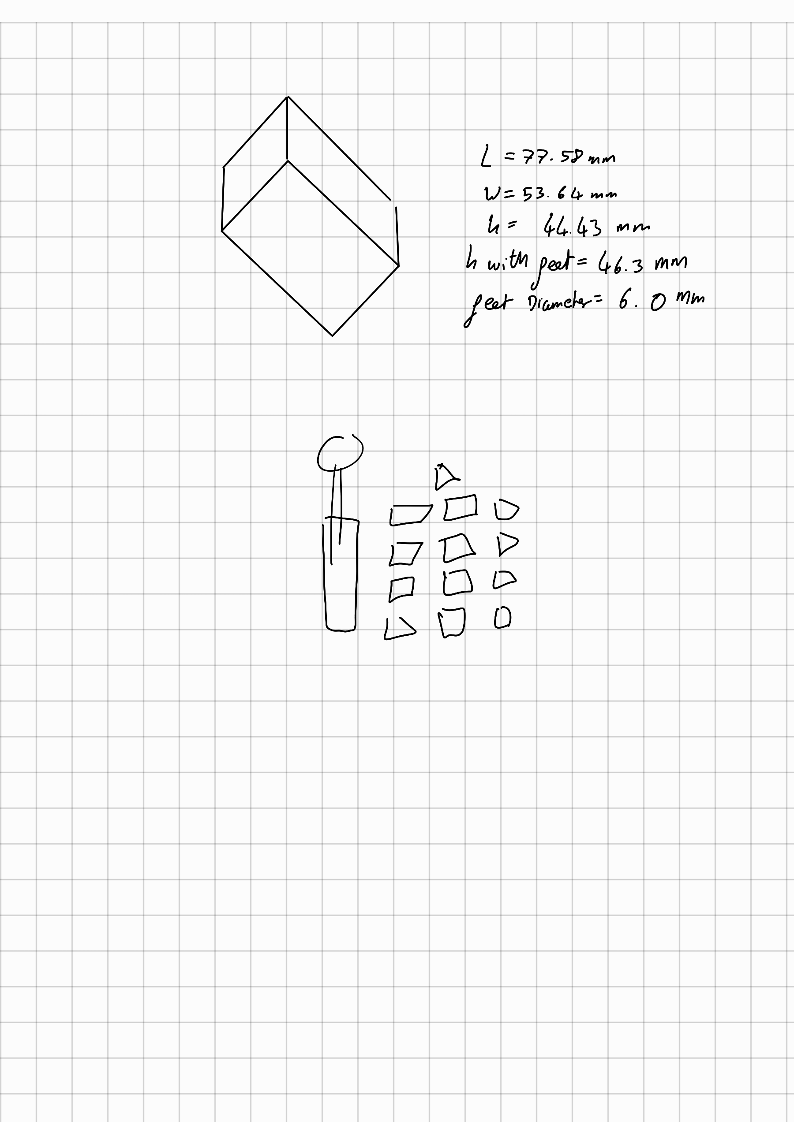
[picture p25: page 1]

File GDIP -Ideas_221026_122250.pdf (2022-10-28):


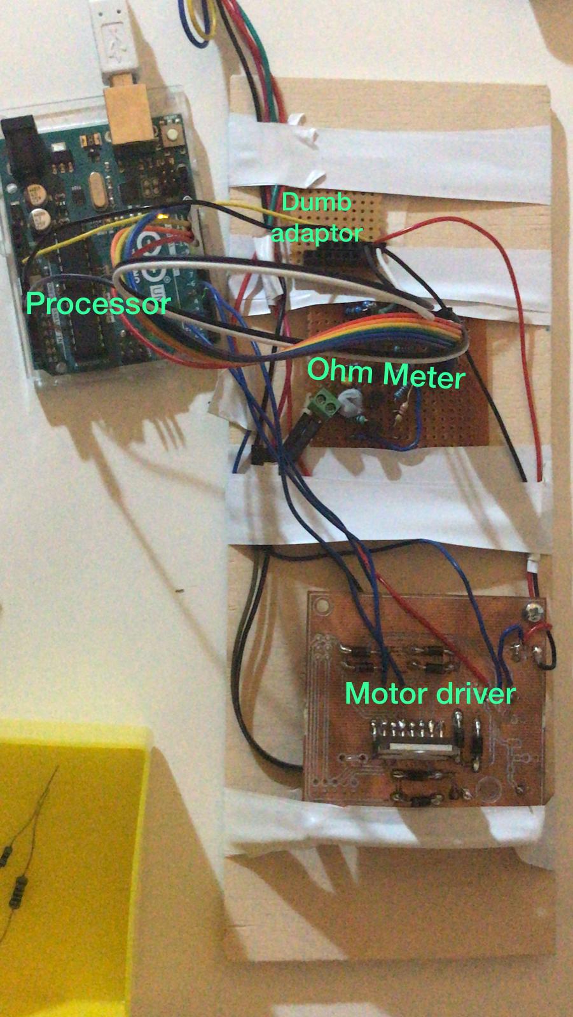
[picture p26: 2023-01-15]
Media/Initial proof of concept for gripper.jpeg

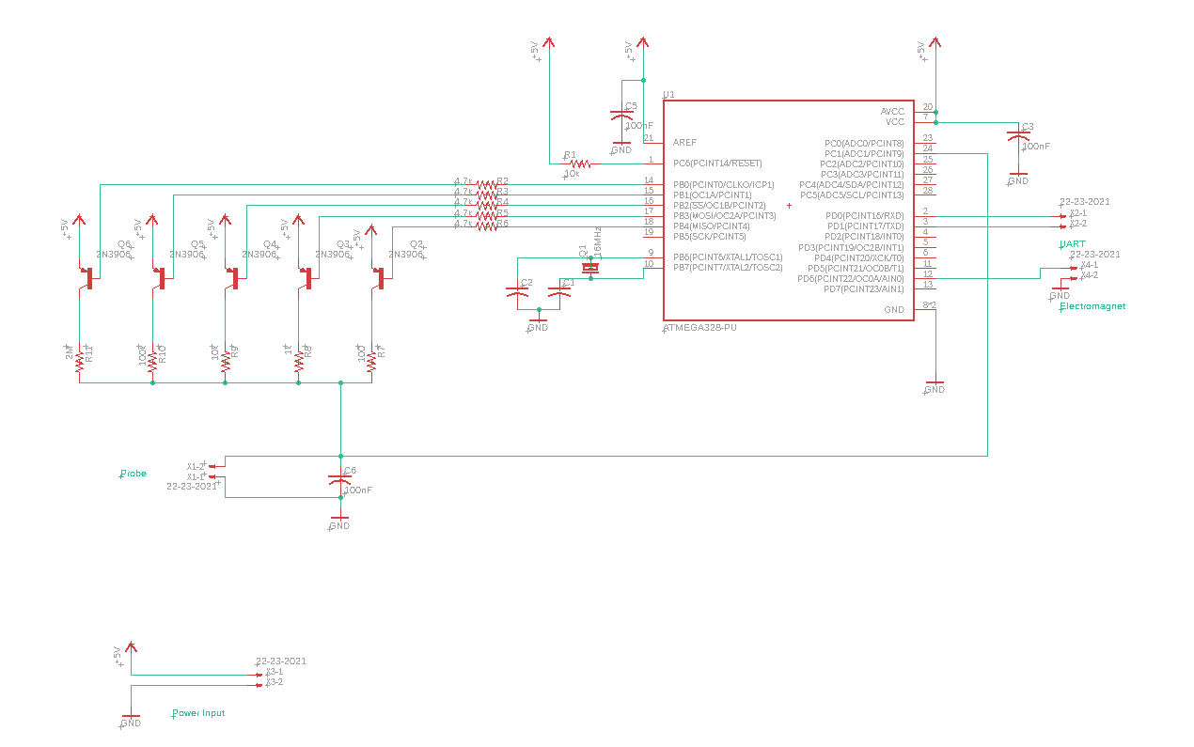
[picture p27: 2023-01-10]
Media/Schematic.png

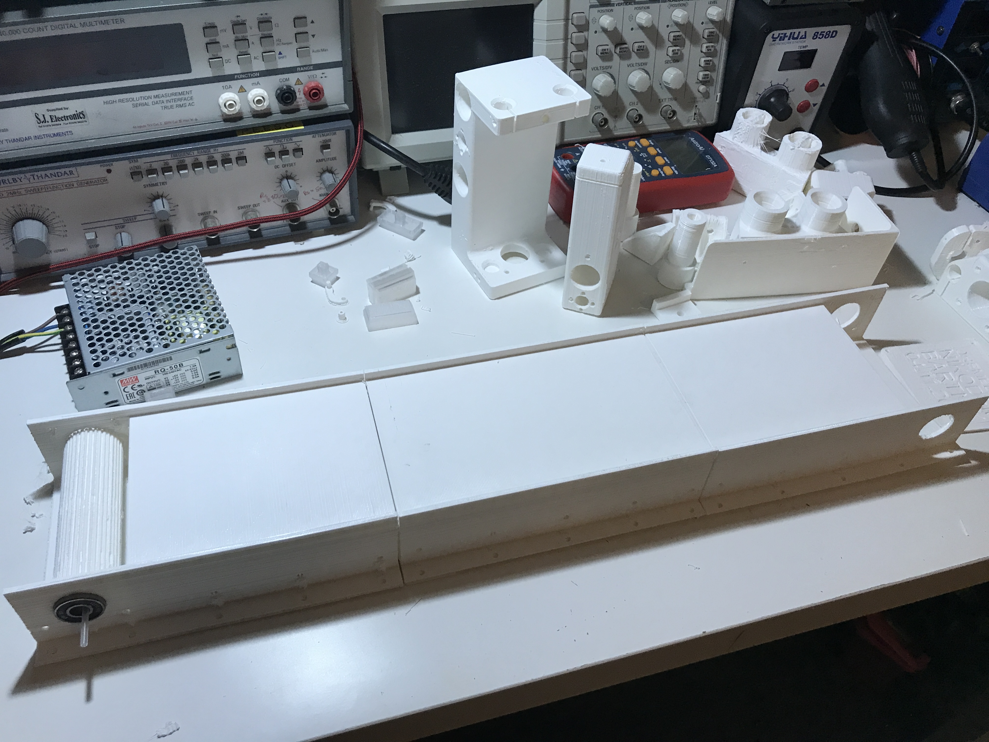
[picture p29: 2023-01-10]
Media/ConveyorBelt.JPG

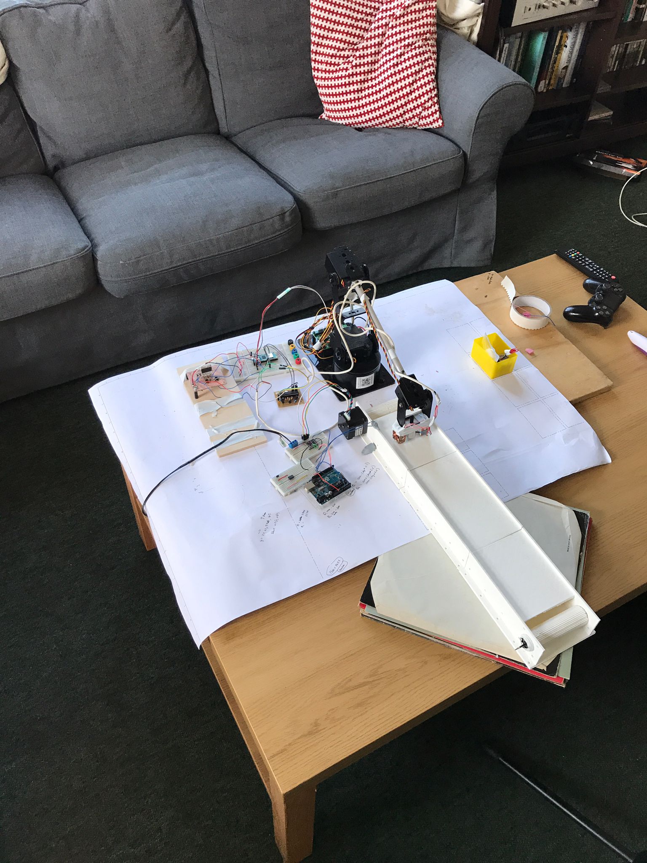
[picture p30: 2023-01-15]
Media/Robot with initial conveyor belt - no base.jpeg

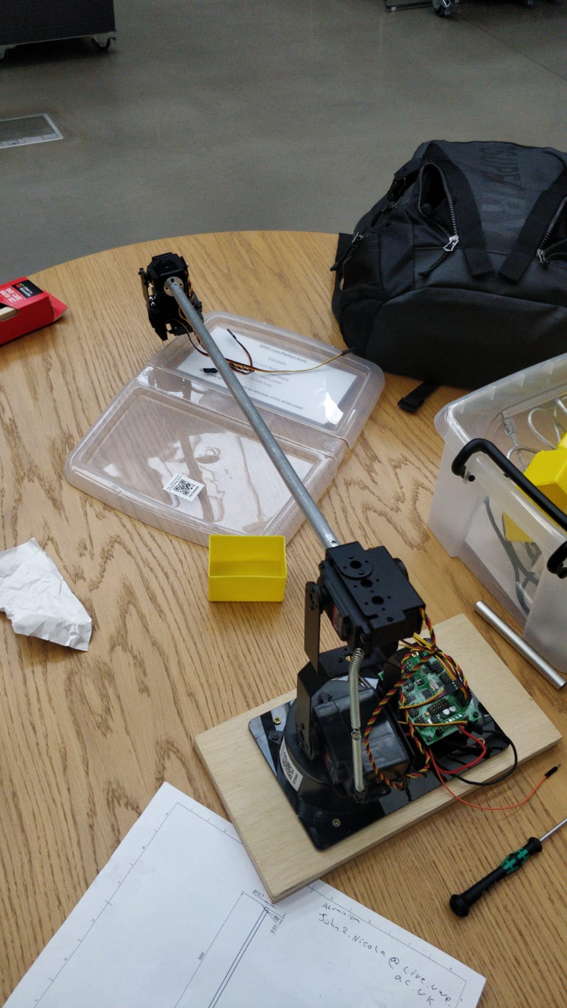
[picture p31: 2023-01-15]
Media/Initial arm extension.jpeg

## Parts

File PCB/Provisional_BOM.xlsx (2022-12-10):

Stepper Motor NEMA 17 | 2 | £12.21 | £14.65 | £29.30 | NO | Digikey | https://www.digikey.co.uk/en/products/detail/adafruit-industries-llc/324/5022791?productid=5022791
Arduino UNO | 1 |  |  |  | YES | RS | https://uk.rs-online.com/web/p/arduino/7154081
ESP32 | 1 |  |  |  | YES | Mouser | https://www.mouser.co.uk/ProductDetail/Espressif-Systems/ESP32-S2-DevKitC-1RU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
Raspberry Pi Pico | 1 |  |  |  | NO | RS | https://uk.rs-online.com/web/p/raspberry-pi/2122162
2N3906 PNP | 10 |  |  |  | NO | Mouser | https://www.mouser.co.uk/ProductDetail/onsemi-Fairchild/2N3906BU?qs=iN0KuJO79Kbn9o7a2lB4uA%3D%3D
16MHz 18pf HC49 | 2 |  |  |  | NO | Mouser | https://www.mouser.co.uk/ProductDetail/ABRACON/ABL-16.000MHZ-B2?qs=A7YjigRBFZlH19Ss3q%252BAbA%3D%3D
HEX SCREW M3 | 1 |  |  |  | NO | RS | https://uk.rs-online.com/web/p/socket-screws/4733530
HEX NUTS M3 | 1 |  |  |  | NO | RS | https://uk.rs-online.com/web/p/hex-nuts/4899450
28PIN DIL SOCK | 1 |  |  |  | NO | Mouser | https://www.mouser.co.uk/ProductDetail/TE-Connectivity/1-2199298-9?qs=fK8dlpkaUMumZ9haKKccEA%3D%3D
Electromagnet 5V 25kg | 1 |  | £10.54 | £10.54 | NO | Farnell | https://uk.farnell.com/dfrobot/dfr0800/electromagnetic-lock-5v-25kg/dp/3769906?mckv=_dc|pcrid||plid||kword||match||slid||product|3769906|pgrid||ptaid|&CMP=KNC-GUK-GEN-SHOPPING-SMART-PMAX-Medium_ROAS-Test958&gross_price=true

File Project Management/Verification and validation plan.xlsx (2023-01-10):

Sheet: Verification and Validation Mat
For requirements and notes see Requirements List document
Requirement ID | Description | Lead team member's | Initial Verification |  |  | Additional Verification |  |  | Stakeholder it links to | Stakeholder sign off | Notes | Key
 |  |  | ID | Type of Verification | Coverage | ID | Type of Verification | Coverage |  |  |  |  | Full Coverage
1 | Minimum Working Envolope | AML & 3DD | 1.1 | Physical | Full | 2.1 | Analytical | Partial | All | UWE fet team |  |  | Partial Coverage
2 | Design a Gripper | PM & 3DD | 4.1 | Review | Full | 1.2 | Physical | Full | University | University |  |  | Inadequate Coverage
3 | Robot Cost XX | EPL & TA | 4.2 | Review | Full |  |  |  | Hobbyist's | Hobbyist's
4 | Measures and moves resistor within 10 seconds | EPL & AML | 3.1 | Code | Partial | 1.3 | Physical | Partial | All | UWE fet team | The two partials overlap to create a full in this case
5 | Be able to sort 12 resitors, and collect all unknow resistors in one location | EPL | 3.2 | Code | Partial | 1.1 | Physical | Partial | All | UWE fet team | The two partials overlap to create a full in this case
6 | 5 Year life span | All | 4.3 | Review | Full |  |  |  | All | UWE fet team
7 | Factor of saftey: 1 | TA & PM | 4.4 | Review | Partial | 1.4 | Physical | Full | University & Labs | UWE fet team
8 | Be ablt to lift 267mg | PM & EPL | 1.5 | Physical | Full |  |  |  | All | University
9 | Sort resistors into the correct box 99% of the time | EPL & AML | 3.3 | Code | Partial | 2.2 | Analytical | Full | All - Uni and labs most | University
10 | Health and saftey documentation | TA | 4.5 | Review | Full |  |  |  | All | UWE fet team
11 | Affordable | All | 4.2 | Review | Full |  |  |  | All | Hobbyist's
12 | Bluetooth | EPL & TA | 2.3 | Analytical | Partial | 3.4 | Code | Partial | All | UWE fet team | The two partials overlap to create a full in this case
13 | App controlled | EPL & PM | 3.5 | Code | Full |  |  |  | Hobbyist's | Hobbyist's
14 | Robot price competative | All | 4.6 | Analytical | Full
 |  |  |  | Project Manager | PM |  |  |  | Document sign off
 |  |  |  | Electronics and Programming lead | EPL |  |  |  | Dominic | James |  | John | Saad | Emre
 |  |  |  | Algorithmic and Mathematical Lead | AML |  |  |  | Yes | Yes |  | Yes | Yes | Yes
 |  |  |  | 3D Design Manager | 3DD
 |  |  |  | Technical Administrator | TA |  |  |  | Stakeholder sign off | Which Stakeholder
 |  |  |  |  |  |  |  |  | Yes | UWE Fet Team

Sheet: Verification ID
Verification ID | Type | Explanation | ID Key
1.1 | Physical | Pulling Arm out to 50cm | 1.x | Physical | Analysis
1.2 | Physical | 3D printing redesigned parts | 2.x | Analysis | Code
1.3 | Physical | Arm can move anywhere in its workling envelope in 5 seconds | 3.x | Code | Review
1.4 | Physical | Arm hold its self together while in use | 4.x | Review from team members
1.5 | Physical | Electromagnet can hold more than one resistor at a time to well over the 267mg required
2.1 | Analysis | Calculating how much arm extension was needed to reach the working envelope
2.2 | Analysis | Code gets the measured resistance correct
2.3 | Analysis | Bluetooth module on the PCB/Arduino
3.1 | Code | Code can measure resistance and decide where the resistor needs to go in 5 seconds | Document sign off
3.2 | Code | Test code can define resistance and tell the arm to move to the correct place | Dominic | James |  | John | Saad | Emre
3.3 | Code | Code gets measured resistance and moves to what it thinks is the correct box | Yes | Yes |  | Yes | Yes | Yes
3.4 | Code | Code can run and be sent using bluetooth
3.5 | Code | Possibility to run code in app |  |  |  |  |  |  | Stakeholder sign off | Which Stakeholder
4.1 | Review from team members | Everyone collaborated on the new gripper design |  |  |  |  |  |  | Yes | UWE Fet Team
4.2 | Review from team members | Everyone agreed and signed off on all orders, documentation was kept
4.3 | Review from team members | All committed to parts which individually are rated over 5 years of use
4.4 | Review from team members | No parts broke due to stress or use
4.5 | Review from team members | Document reviewed by all and meets standards
4.6 | Review from team members | A financial plan is produced

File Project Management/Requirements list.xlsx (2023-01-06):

For Verification and validation see Verification and Validation plan document |  |  |  |  |  |  | Which System level its tracable from
Requirement ID | List of Requirements | Source | Notes | Succsess | Failure | Additional Notes
1 | Minimum Working Envolope | Project Brief | Defined as 50cm | Shorterned the car and hollowed out more of it to decrease weight, still reach the 50cm working envelope | - Had a new bar made which was too long and heavy |  | Able to sort all E12 resistors - Ease of use - Worth purchacing
2 | Design a gripper | Project Brief | Has to pickup a resistor | Can pick up the resitor |  |  | Safe - Gripper can pick up resistor - Worth purchacing
3 | Robot price competative | Stakeholder | Budget limmitation | We didnt go over the budget |  |  | Worth purchasing
4 | Measures and moves resistor within 10 seconds | Stakeholder - University |  | Can do it in sub 10 seconds |  |  | Ease of use - Worth purchasing
5 | Be able to sort 12 resitors, and collect all unknow resistors in one location | Stakeholders | All E12 resistors should be sorted with any additional beeing seperated | Acheved |  |  | Ease of use - Worth purchasing
6 | 5 Year lifetime | Stakeholder - Labs | We cant test this but through the verification and validation plan the reliability can be shown | Acheved |  | All parts are rates for greater than 5 years of use under certain conditions | Worth purchasing - Safe
7 | Factor of safety : 1 | Stakeholder - Labs | Not a strugtual part so has a low FoS | Acheved |  |  | Safe
8 | Be ablt to lift 267mg | Stakeholders | This is the average weight of an E12 resistor | We were able to lift the resistor |  |  | Worth purchasing
9 | Sort resistors into the correct box 99% of the time | Stakeholders | This is essentally 100% but validating 100% correct sorting is impossible | Through testing the robot was correct all the time |  |  | Able to sort all E12 resistors - Ease of use - Worth purchacing
10 | Health and saftey documentation | Stakeholders | To go with every order | Curated and included in files |  |  | Safe
11 | Affordable | Stakeholders | Not much more expensive than the base arm | Under budget |  |  | Worth Purchasing
12 | Bluetooth | Stakeholders | Dont need to be connected to the arm by a wire |  | Not able to complete this on the first prototype but theoretically tested and works | Ordered | Ease of use
13 | App controlled | Stakeholders | possibility to use your phone to controll the arm |  | Unfortunately out of scope for the MVP but app integration will be simple once Bluetooth is working |  | Ease of use
 |  |  |  |  | Stakeholder sign off | Which Stakeholder
 |  |  |  |  | Yes | UWE Fet Team and Hobbyists
 |  |  |  |  | Document Sign off
 |  |  |  |  | Dominic | James | John | Saad | Emre
 |  |  |  |  | Yes | Yes | Yes | Yes | Yes

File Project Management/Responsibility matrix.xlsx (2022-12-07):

Name | Role | Project Initiation |  |  | Project Planning |  |  |  |  | Project Development |  |  |  |  |  |  |  |  |  |  |  | Project Close
 |  | Define Scope | Define Roles | Define stakeholders | Define Design Requiremenmts | Financial Plan | Health and Saftey Plan | Interlectual Property Protection | Select bought components | Design Electrical Components | Program Arm | Test Electrical Components | Calculate Arm Geometry | Modify Arm | Test Arm | Design Gripper | Model Gripper in CAD | Manufacture and fit Gripper | Assemble Mimimum Viable Product (MVP) | Test MVP in set conditions | Test MVP in not set conditions | Set up production line | Build first batch
Dominic | Project Manager | R | R | R | A | A | C | C | A | C | I | I | C | C | A | C | R | C | A | R | R | A | A | Dominic | Key
James | Electronics and Programming Lead | R |  | C | R | C |  | I | R | R | R | R |  |  | R |  | C | C | R | R | R | C | C | James | R = RESPONSIBILITY
John | 3D Design and Mechanical Manager | R |  | C | R | C | I | I | R | I | C |  | A | R | R | R | C | R | R | R | R | C | C | John | A = ACCOUNTABILITY
Saad | Algorithmic and mathematical Lead | R |  | C | R | C |  | I | C | I | C |  | R | A | R | C | I | I | I | R | R | C | C | Saad | C = CONSULTATION
Emre | Technical Advisor | R |  | C | R | R | R | R | I |  |  |  | I |  | I |  | I |  | I | R | R | R | R | Emre | I = INFORMATION
 | Key
 | R = RESPONSIBILITY
 | A = ACCOUNTABILITY
 | C = CONSULTATION
 | I = INFORMATION

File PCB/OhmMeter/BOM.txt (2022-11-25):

Partlist exported from C:/Users/jimbo/Documents/GitHub/GDIP_ROBOT/PCB/OhmMeter/OhmMeter.sch at 25/11/2022 05:41

Qty Value        Device          Package                   Parts              Description                                                                                      AVAILABILITY DESCRIPTION                                                                    MF                   MP           MPN        OC_FARNELL OC_NEWARK PACKAGE                     POPULARITY PRICE PURCHASE-URL                                                 
2                C-US025-024X044 C025-024X044              C1, C2             CAPACITOR, American symbol                                                                                                                                                                                                                                                                                                                                               
1   100          R-US_0204/5     0204/5                    R7                 RESISTOR, American symbol                                                                                                                                                                                                                                                                                                                                                
1   100k         R-US_0204/5     0204/5                    R10                RESISTOR, American symbol                                                                                                                                                                                                                                                                                                                                                
3   100nF        C-US025-024X044 C025-024X044              C3, C5, C6         CAPACITOR, American symbol                                                                                                                                                                                                                                                                                                                                               
2   10k          R-US_0204/5     0204/5                    R1, R9             RESISTOR, American symbol                                                                                                                                                                                                                                                                                                                                                
1   16MHz        CRYSTALHC49S    HC49/S                    Q1                 CRYSTAL                                                                                                                                                                                                                                   1667008    unknown                                                                                                             
1   1k           R-US_0204/5     0204/5                    R8                 RESISTOR, American symbol                                                                                                                                                                                                                                                                                                                                                
4   22-23-2021   22-23-2021      22-23-2021                X1, X2, X3, X4     .100" (2.54mm) Center Header - 2 Pin                                                                                                                                                         MOLEX                             22-23-2021 1462926    25C3832                               40                                                                            
1   2M           R-US_0204/5     0204/5                    R11                RESISTOR, American symbol                                                                                                                                                                                                                                                                                                                                                
5   2N3906       2N3906          TO92                      Q2, Q3, Q4, Q5, Q6 PNP Transistor                                                                                                                                                                                                                                                                             11                                                                            
5   4.7k         R-US_0204/5     0204/5                    R2, R3, R4, R5, R6 RESISTOR, American symbol                                                                                                                                                                                                                                                                                                                                                
1   ATMEGA328-PU ATMEGA328-PU    DIP787W46P254L3467H508Q28 U1                 AVR AVR® ATmega Microcontroller IC 8-Bit 20MHz 32KB (16K x 16) FLASH 28-PDIP  Check availability In Stock      AVR AVR® ATmega Microcontroller IC 8-Bit 20MHz 32KB (16K x 16) FLASH 28-PDIP  Microchip Technology ATMEGA328-PU                                 DIP-28 Microchip Technology            None  https://pricing.snapeda.com/search/part/ATMEGA328-PU/?ref=eda

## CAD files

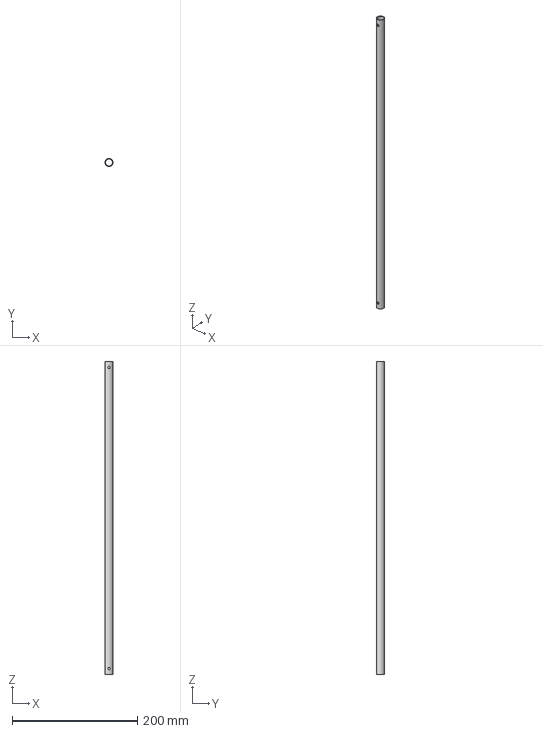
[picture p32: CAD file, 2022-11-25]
Arm_Extension/At-03 arm extention John v1 v1.step
12.7 x 12.7 x 500.0 mm

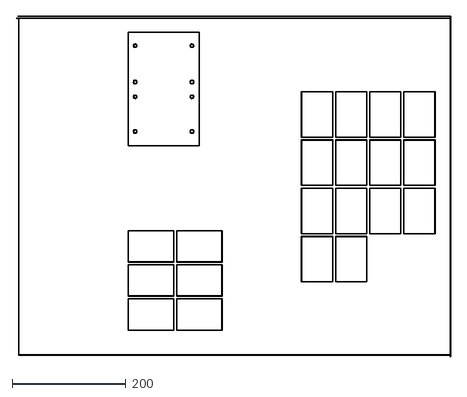
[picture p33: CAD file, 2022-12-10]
Base/JamesOhare_Basev5_6mmMDF_RedCut_BlackEngrave.dxf
764.8 x 600.0

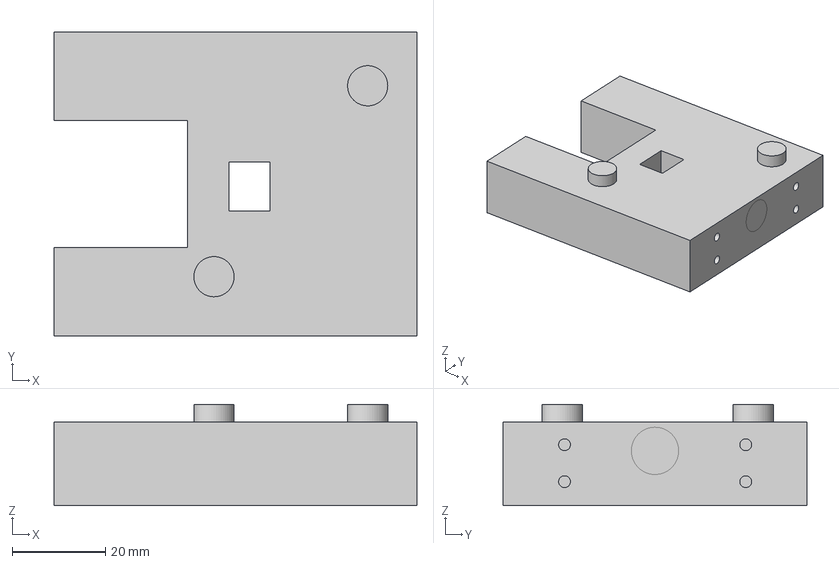
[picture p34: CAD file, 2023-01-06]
Gripper/GRIPPER_FINAL.step
78.0 x 65.4 x 21.8 mm

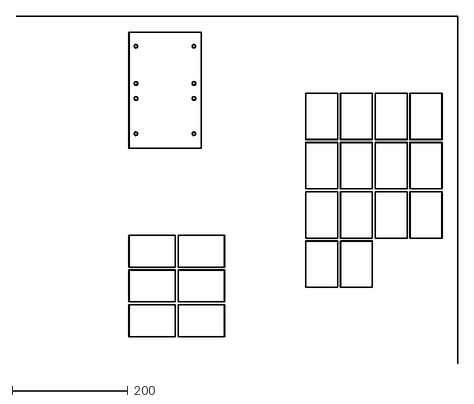
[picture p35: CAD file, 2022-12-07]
Base/JamesOhare_6mmMDF_RedCut_BlackEngrave.dxf
762.3 x 600.0

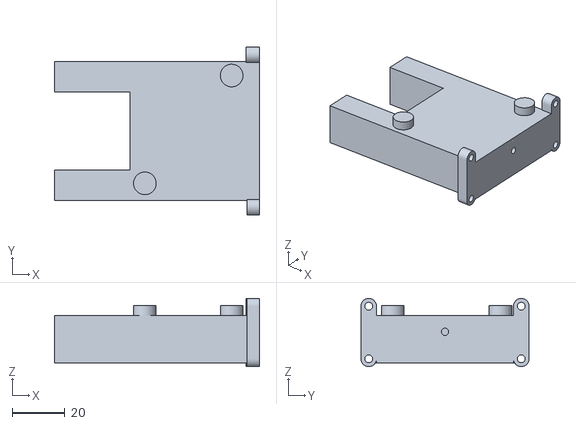
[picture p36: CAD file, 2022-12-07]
Gripper/PCBMountingSection.stl
78.0 x 64.0 x 25.9

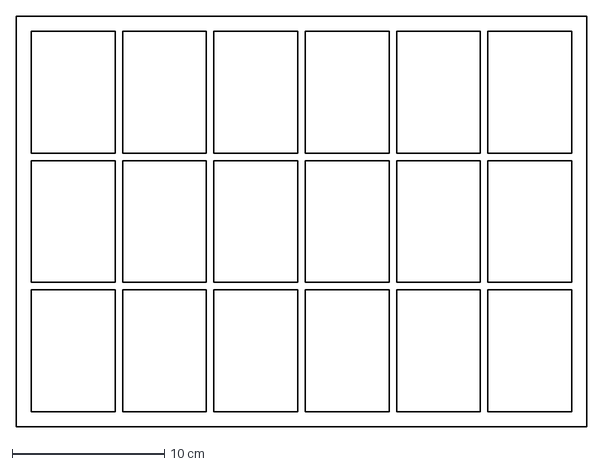
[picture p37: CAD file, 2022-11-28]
Gripper/Base v1DXF.dxf
37.5 x 27.0 cm

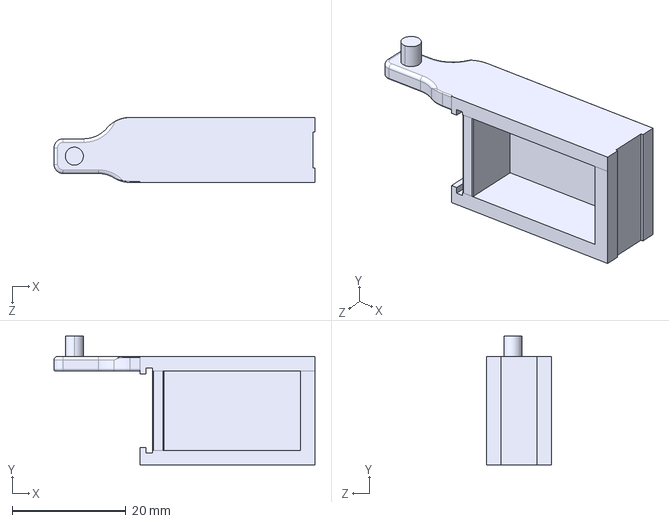
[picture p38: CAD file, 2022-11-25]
Gripper/Right gripper.STEP
45.9 x 22.6 x 11.5 mm

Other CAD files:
Gripper/Base v1.step
Gripper/Base v1DWGDWG.dwg
Gripper/Left gripper.STEP
Base/Base v5 v1.f3d
Gripper/Base v1.f3d
Gripper/GRIPPER_FINAL.f3d
Gripper/GRIPPER_OLD_V2.f3d
Gripper/Gripper.f3z
Gripper/Gripper_old_old_V1.f3d
Gripper/Left gripper.SLDPRT
Gripper/Left_gripper_old_old_old_V1.f3d
Gripper/Right gripper.SLDPRT
PCB/OhmMeter/asb-09 v5.f3z

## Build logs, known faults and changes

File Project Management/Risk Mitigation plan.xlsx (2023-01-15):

Severity |  |  |  |  |  |  | Risk | Implication | Severity | Likelihood | Risk Rating | Risk Mitigation Plan
Catastrophic | 5 | 5 | 10 | 15 | 20 | 25 | - | - | 5 | 5 | 25
Significant | 4 | 4 | 8 | 12 | 16 | 20 | - | - |  |  | 0
Moderate | 3 | 3 | 6 | 9 | 12 | 15 | Management Risks
Low | 2 | 2 | 4 | 6 | 8 | 10 | Lack of Validation and Verification | Product isn't acceptable to Investors | 5 | 1 | 5 | Develop a robust Verification and Validation Plan, UPDATE - Plan was created lowering the liklily hood
Negligible | 1 | 1 | 2 | 3 | 4 | 5 | Delay in planning process | Delay in project end date | 3 | 3 | 9 | Allow upper and lower bounds in project time
 |  | 1 | 2 | 3 | 4 | 5 | Technical risks
Likelihood |  | Improbable | Remote | Occasional | Probable | Frequent | Design error | End product does not meet requirements | 5 | 1 | 5 | Verification plan
 |  |  |  |  |  |  | Arm doesnt meet minimum Specification | Not what the customer requires | 4 | 1 | 4 | Create a clear Stakeholder requiremenmts diagram and use the verification plan
 |  |  |  |  |  |  | Collapse in the semiconductor market | Cant use a certain type of chip | 2 | 3 | 6 | Create a solution that could work with many different standards so more than one typr of tech nology could be convereted for use in the project
Key |  |  |  |  |  |  | Software malfunction | Arm doesnt complete the required task | 4 | 1 | 4 | Extensive testing of software and hardware, verification plan
Green | Minor Risk Mitigation Plan needed |  |  |  |  |  | Legal and Contractual
Yellow | Modirate Risk Mitigation Plan needed |  |  |  |  |  | Patent Infringement | Liable to legal action | 4 | 1 | 4 | Follow legal requirements and keep all documentation, part of the Validation plan
Orange | Significant risk mitigation plan needed |  |  |  |  |  | Corporate espionage | Loss of money, lower profits | 4 | 1 | 4 | NDA contracts, dispose correctly of legal documents
Red | Have a Comprehensive Risk mitigation plan |  |  |  |  |  | Economic
 |  |  |  |  |  |  | Increase in mirco-chip cost | Increase in parts cost, lowering proffits | 3 | 1 | 3 | Use off the shelf components, run the arm on as little compute as possible so what chip is used is of limmited significance
 |  |  |  |  |  |  | Unproportional increase in interest rates | Lower budget, liquidation | 3 | 1 | 3 | Insure loans against the market, assuming borrowing to start up the company
 |  |  |  |  |  |  | Insufficient lifetime funding | delay in project end date, termination | 4 | 1 | 4 | Have multiply revenue streams
Document sign off |  |  |  |  |  |  | Market
Dominic | James |  | John | Saad | Emre |  | No longer a desired product | Lower sales than necessary, start up colapses | 5 | 1 | 5 | Keep in constant contact with stakeholders to insure the product is desirable to them
Yes | Yes |  | Yes | Yes | Yes |  | Strong competition | Lack of sales, leading to lower profit | 3 | 4 | 12 | Have a superior product
 |  |  |  |  |  |  | Health and Safety
 |  |  |  |  |  |  | Global Pandemic | Inability to meet in person | 5 | 2 | 10 | Verification and Verification plan that works online, have online meetings, use Github so all files are readily accessable by everone
 |  |  |  |  |  |  | Mechanical injury/Arm colliding with a person | Legal action, loss of profits, delay in project | 4 | 3 | 12 | Outline necessary health and saftely plan fopr customers, limmit the potential speed nad torque of the arm

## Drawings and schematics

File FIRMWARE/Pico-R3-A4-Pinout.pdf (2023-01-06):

# Raspberry Pi Pico Pinout

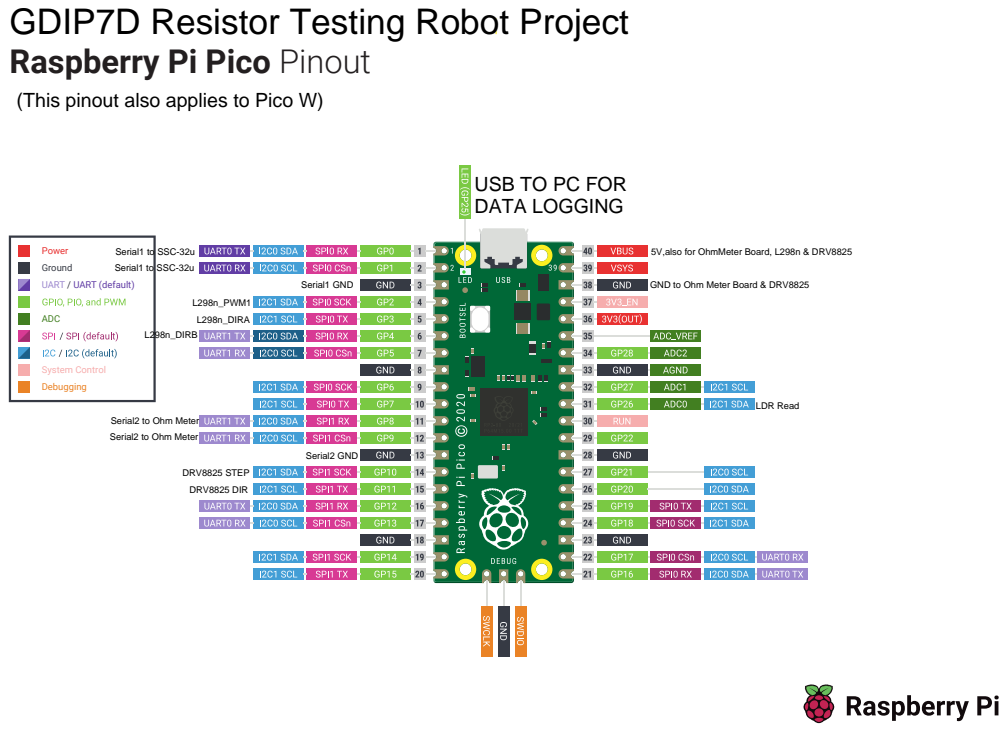
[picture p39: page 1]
System Control Debugging; ADC

Power
Ground
UART / UART (default)

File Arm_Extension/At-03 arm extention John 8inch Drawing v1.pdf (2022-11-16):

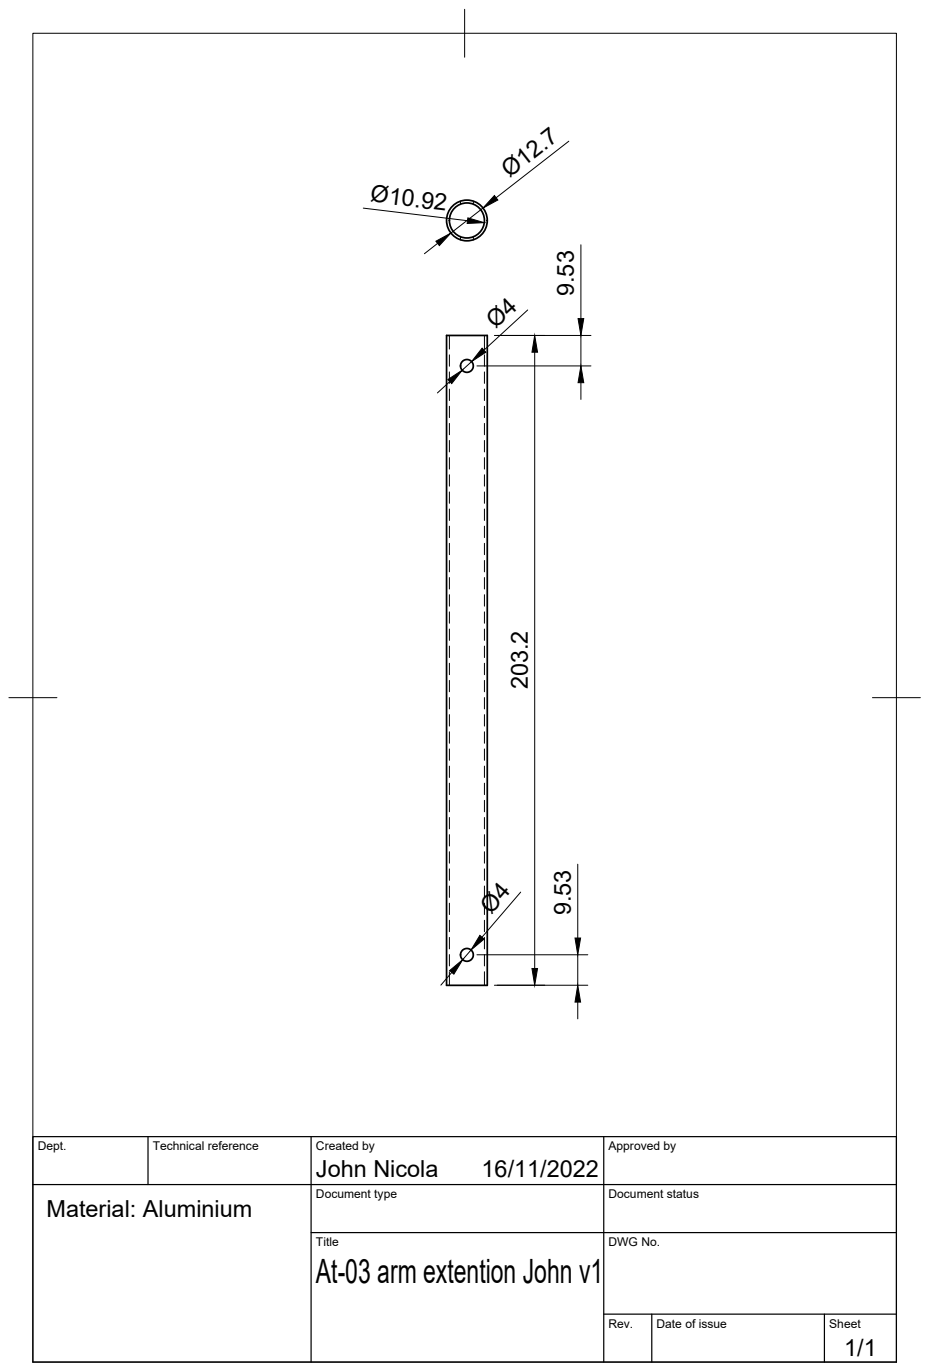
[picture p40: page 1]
John Nicola

Dept. | Technical reference | Created by 16/11/2022 | Approved by

Material: Aluminium | | Document type | Document status

Title At-03 arm extention John v1 | DWG No.

Rev. | Date of issue | Sheet 1/1

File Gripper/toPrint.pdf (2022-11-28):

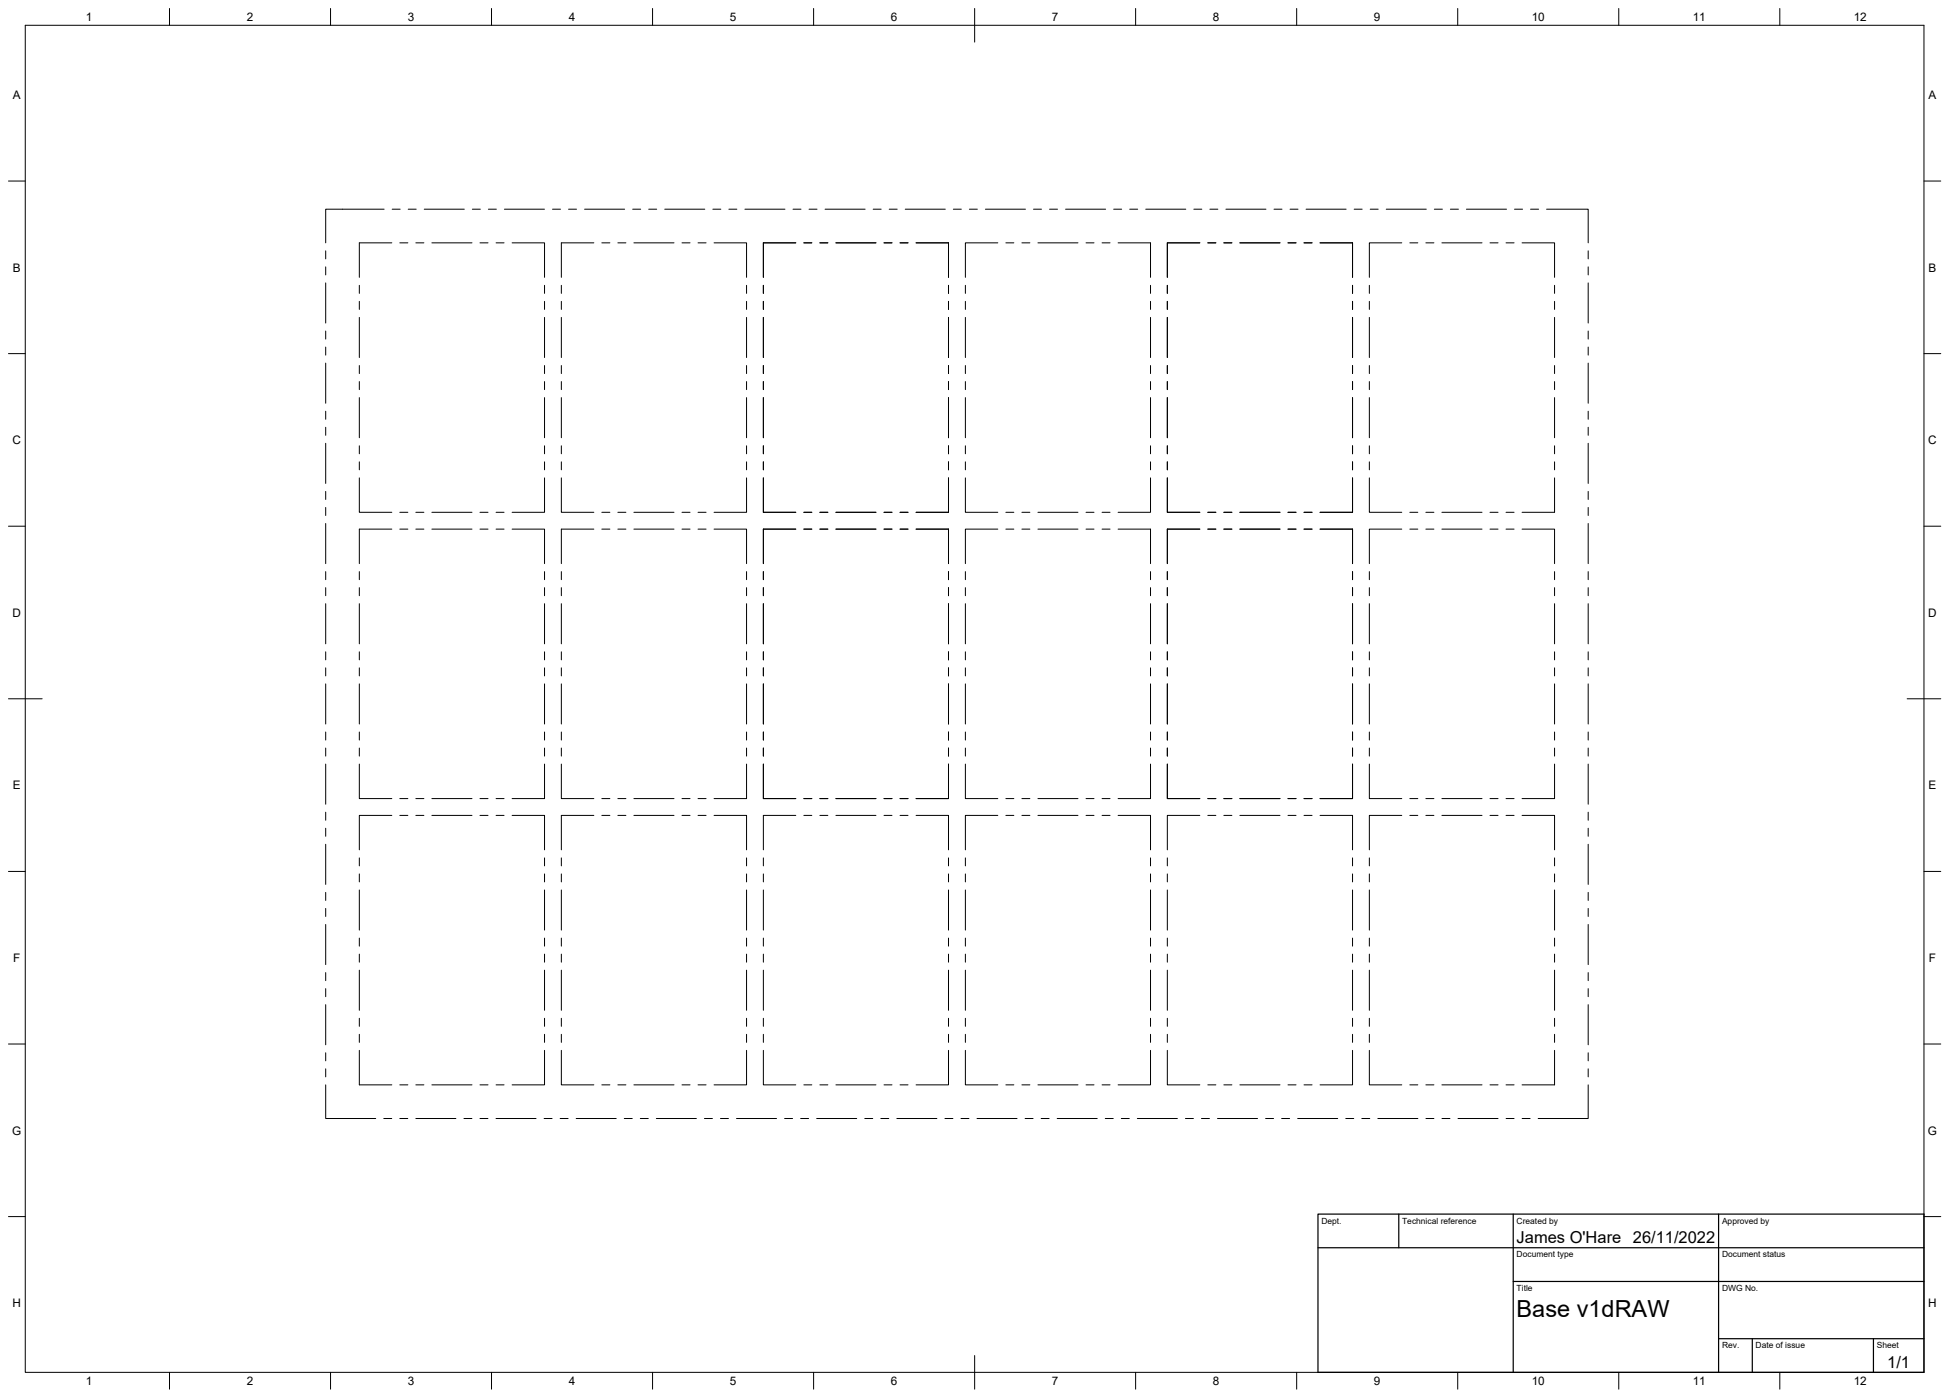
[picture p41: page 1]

Dept. | Technical reference | Created by James O'Hare 26/11/2022 | Approved by

Document type | Document status

Title Base v1dRAW | DWG No.

Rev. | Date of issue | Sheet 1/1

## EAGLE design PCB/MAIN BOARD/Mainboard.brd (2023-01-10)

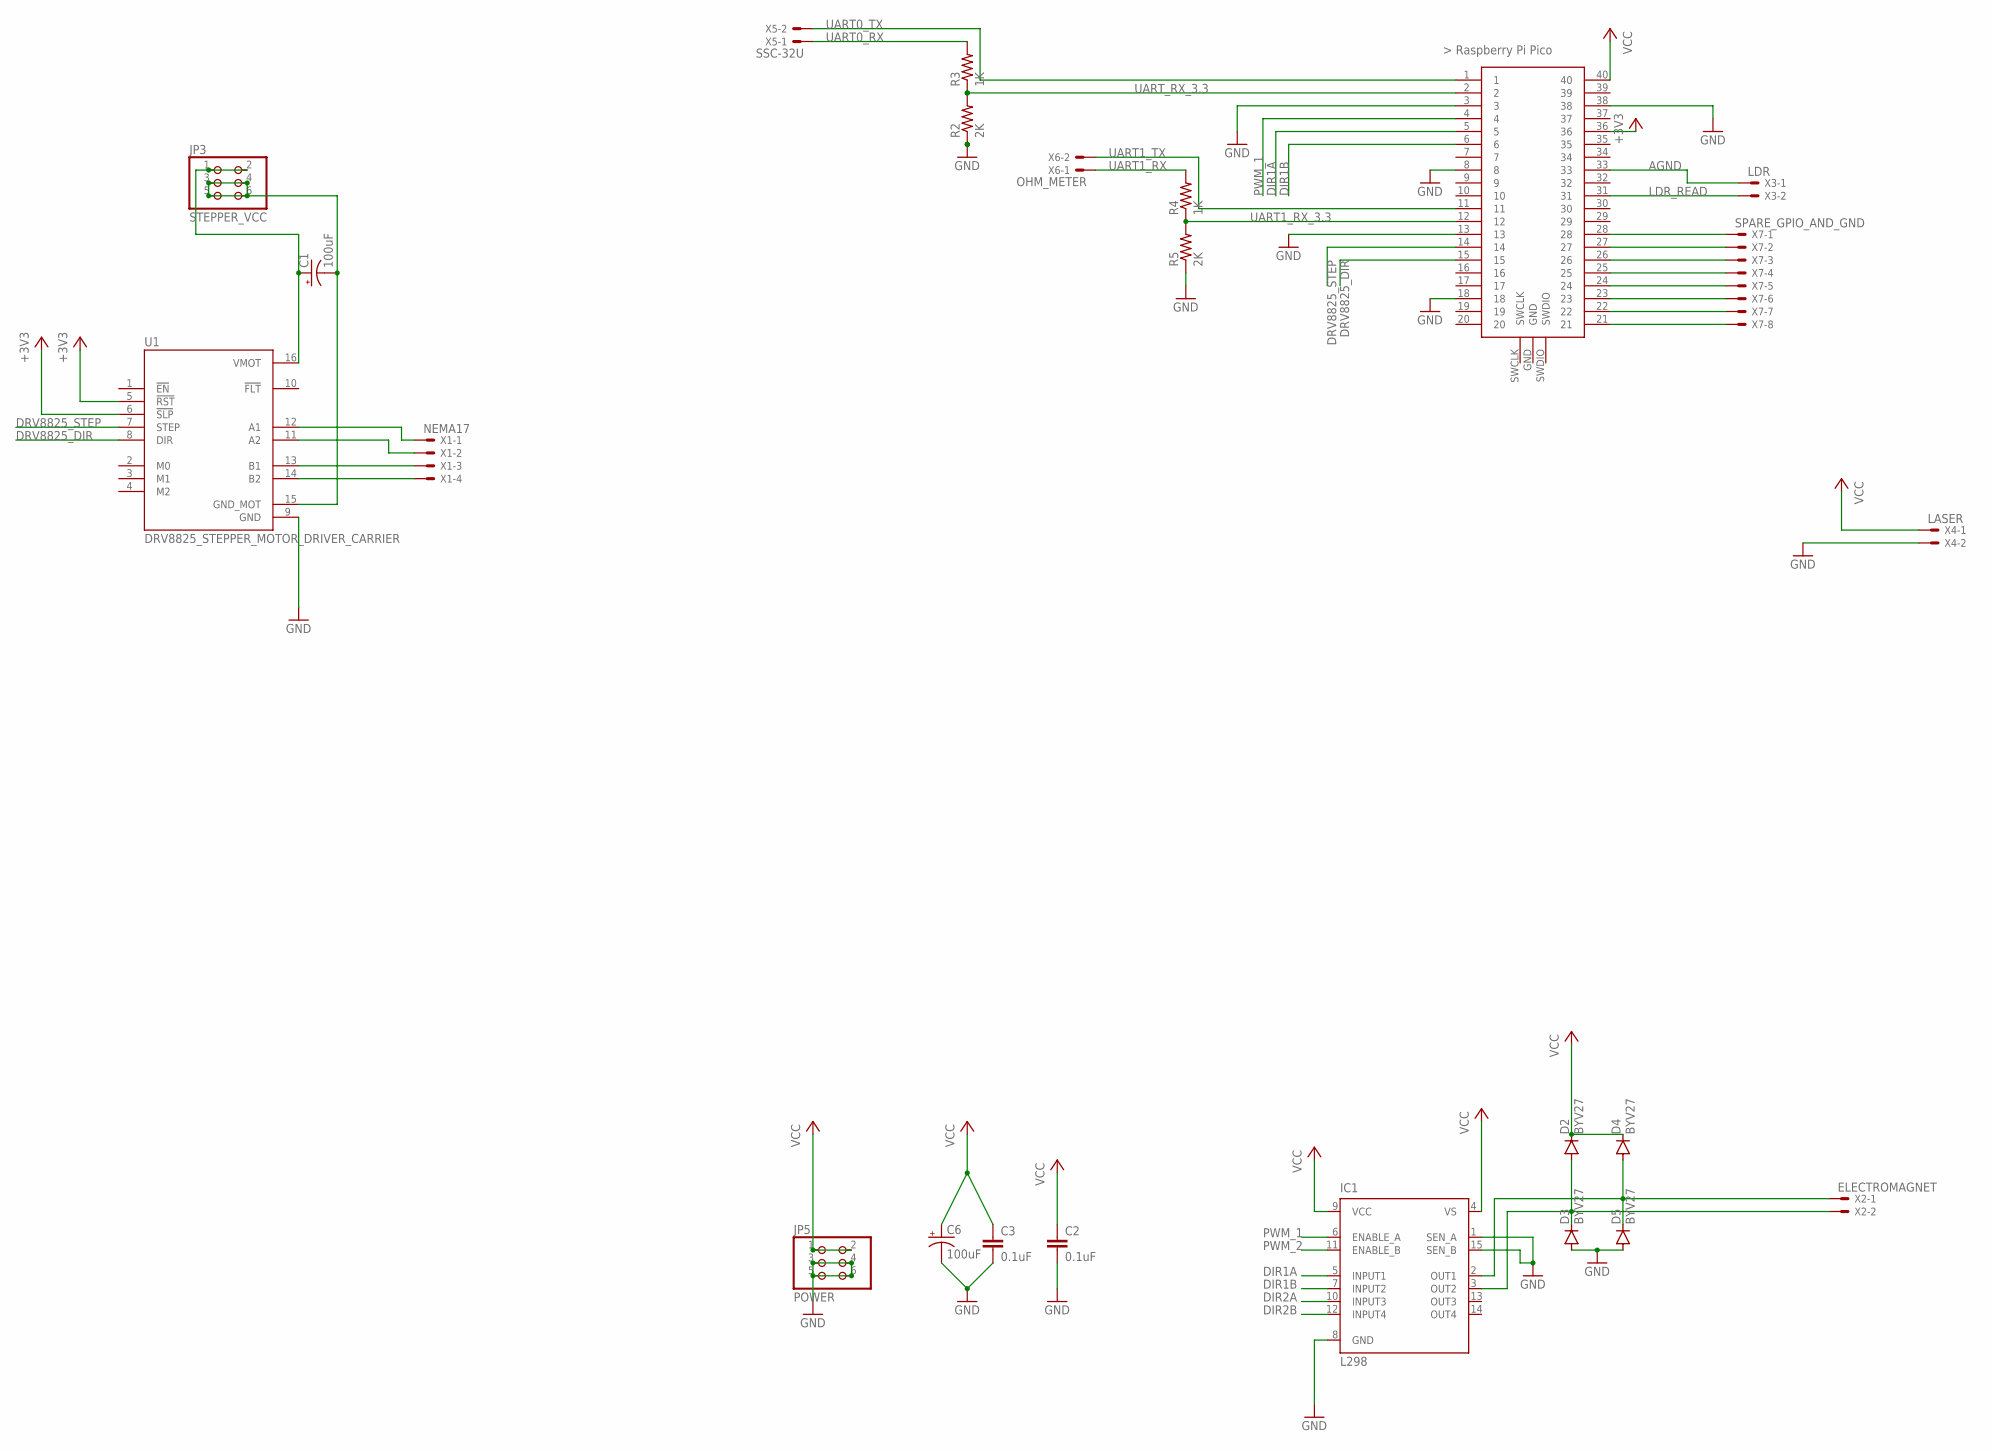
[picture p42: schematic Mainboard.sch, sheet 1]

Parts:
C1, C6: 100uF; CPOL-RADIAL-2.5MM-6.5MM
C2, C3: 0.1uF; 0603
D2, D3, D4, D5: BYV27; SOD57-10
IC1: L298; MULTIWATT-15
JP3: STEPPER_VCC; 2X03
JP5: POWER; 2X03
R2, R5: 2K; R0603
R3, R4: 1K; R0603
U1: DRV8825_STEPPER_MOTOR_DRIVER_CARRIER; IC_DRV8825_STEPPER_MOTOR_DRIVER_CARRIER
U$1: RASPBERRY-PI-PICO_W; FT_RASPBERRY-PI-PICO_TH
X1: NEMA17; 22-23-2041
X2: ELECTROMAGNET; 22-23-2021
X3: LDR; 22-23-2021
X4: LASER; 22-23-2021
X5: SSC-32U; 22-23-2021
X6: OHM_METER; 22-23-2021
X7: SPARE_GPIO_AND_GND; 22-23-2081

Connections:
+3V3: U1.5 (!RST), U1.6 (!SLP), U$1.36
+5V: C2.1, IC1.9 (VCC)
AGND: U$1.33, X3.1
DIR1A: IC1.5 (INPUT1), U$1.5
DIR1B: IC1.7 (INPUT2), U$1.6
DIR2A: IC1.10 (INPUT3)
DIR2B: IC1.12 (INPUT4)
DRV8825_DIR: U1.8 (DIR), U$1.15
DRV8825_STEP: U1.7 (STEP), U$1.14
GND: C2.2, C3.2, C6.2 (-), D3.A, D5.A, IC1.1 (SEN_A), IC1.8 (GND), IC1.15 (SEN_B), JP5.3, JP5.4, JP5.5, JP5.6, R2.1, R5.1, U1.9 (GND), U$1.3, U$1.8, U$1.13, U$1.18, U$1.38, X4.2
LDR_READ: U$1.31, X3.2
MOTOR_1_+: D4.A, D5.C, IC1.2 (OUT1), X2.1
MOTOR_1_-: D2.A, D3.C, IC1.3 (OUT2), X2.2
unnamed: C1.1 (+), JP3.1, JP3.2, U1.16 (VMOT)
unnamed: C1.2 (-), JP3.3, JP3.4, JP3.5, JP3.6, U1.15 (GND_MOT)
unnamed: U1.12 (A1), X1.1
unnamed: U1.11 (A2), X1.2
unnamed: U1.13 (B1), X1.3
unnamed: U1.14 (B2), X1.4
unnamed: U$1.21, X7.8
unnamed: U$1.22, X7.7
unnamed: U$1.25, X7.4
unnamed: U$1.23, X7.6
unnamed: U$1.24, X7.5
unnamed: U$1.26, X7.3
unnamed: U$1.27, X7.2
unnamed: U$1.28, X7.1
PWM_1: IC1.6 (ENABLE_A), U$1.4
PWM_2: IC1.11 (ENABLE_B)
UART0_RX: R3.2, X5.1
UART0_TX: U$1.1, X5.2
UART1_RX: R4.2, X6.1
UART1_RX_3.3: R4.1, R5.2, U$1.12
UART1_TX: U$1.11, X6.2
UART_RX_3.3: R2.2, R3.1, U$1.2
VCC: C3.1, C6.1 (+), D2.C, D4.C, IC1.4 (VS), JP5.1, JP5.2, U$1.40, X4.1

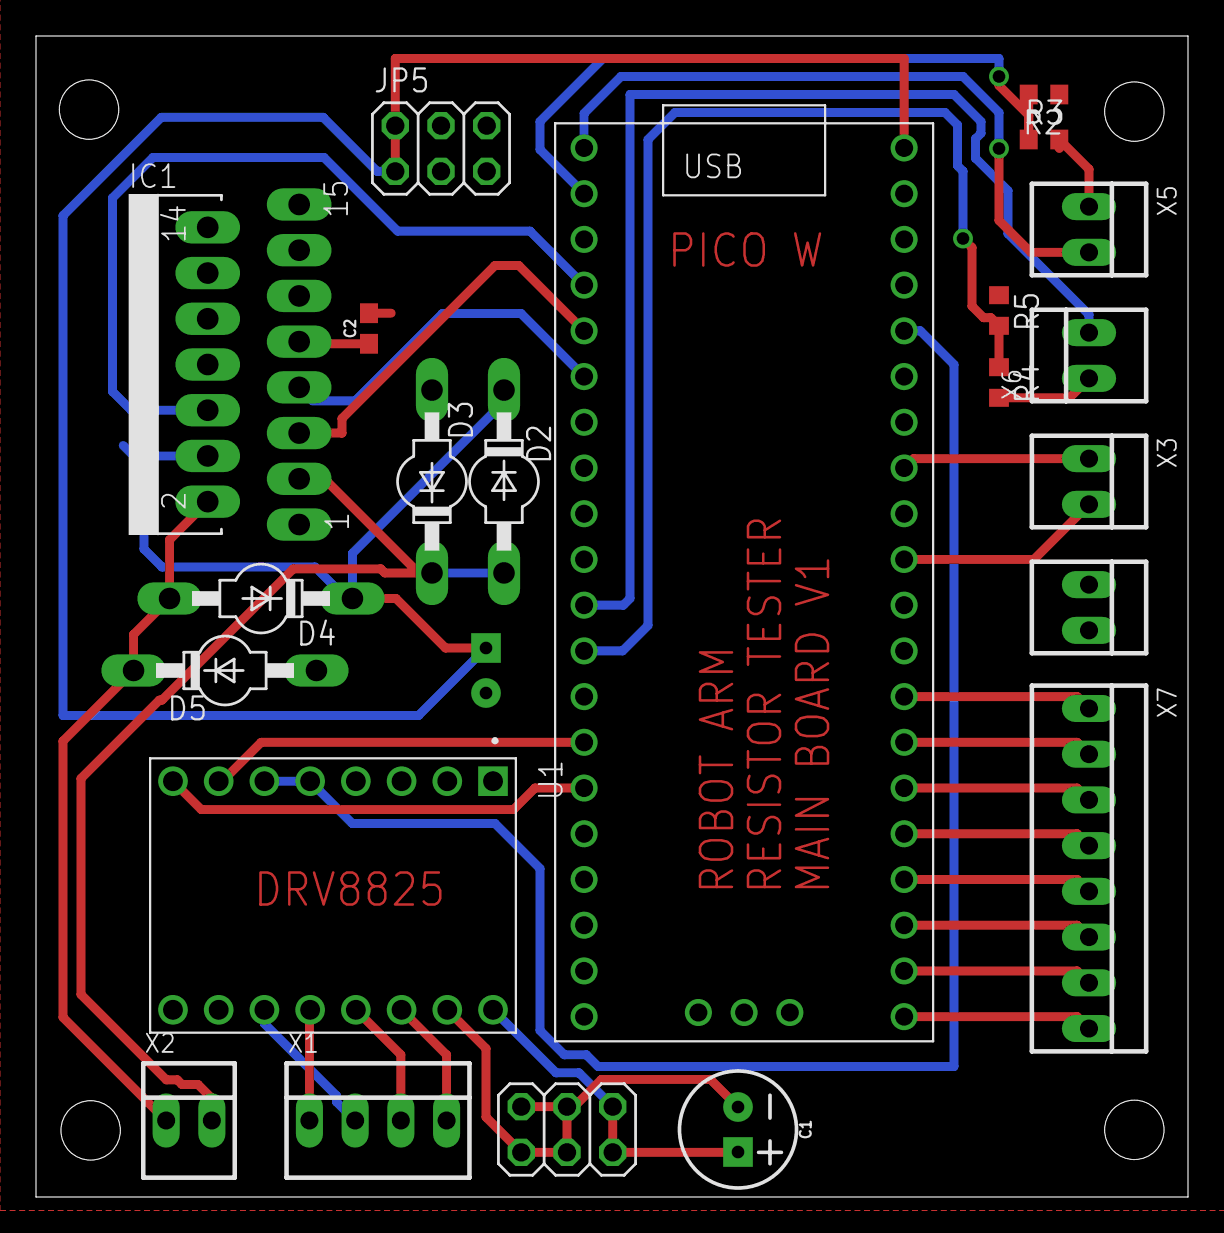
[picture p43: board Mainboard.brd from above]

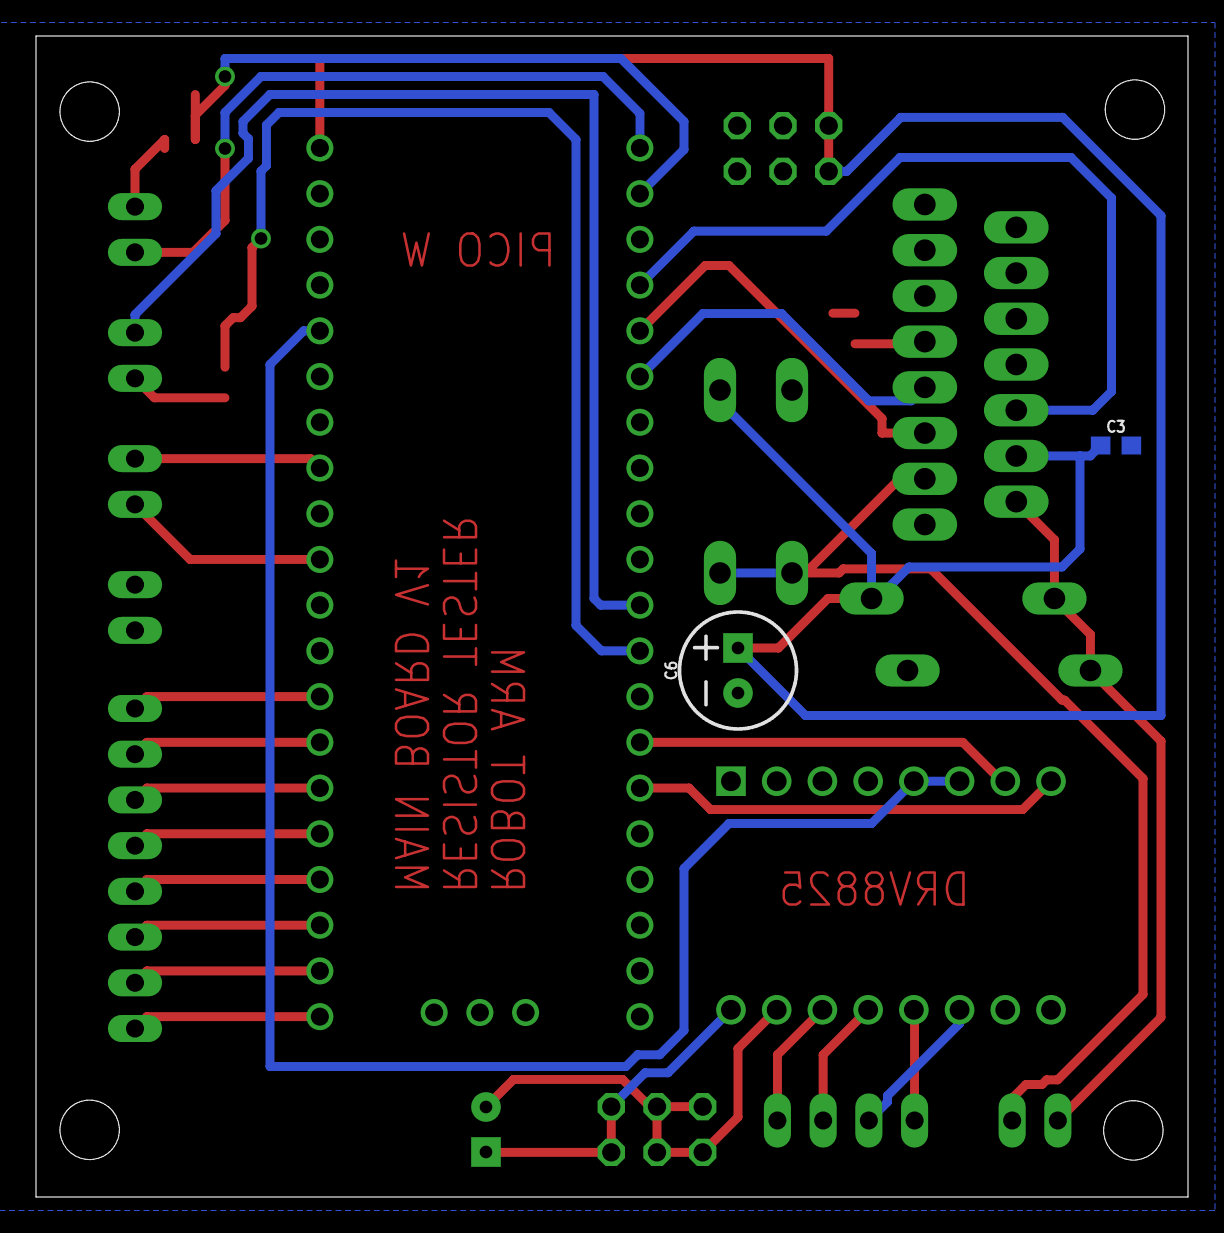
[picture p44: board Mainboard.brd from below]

Board: 2 copper layers, 64.0 x 64.5 mm, 24 parts (2 on the bottom side), 33 nets.

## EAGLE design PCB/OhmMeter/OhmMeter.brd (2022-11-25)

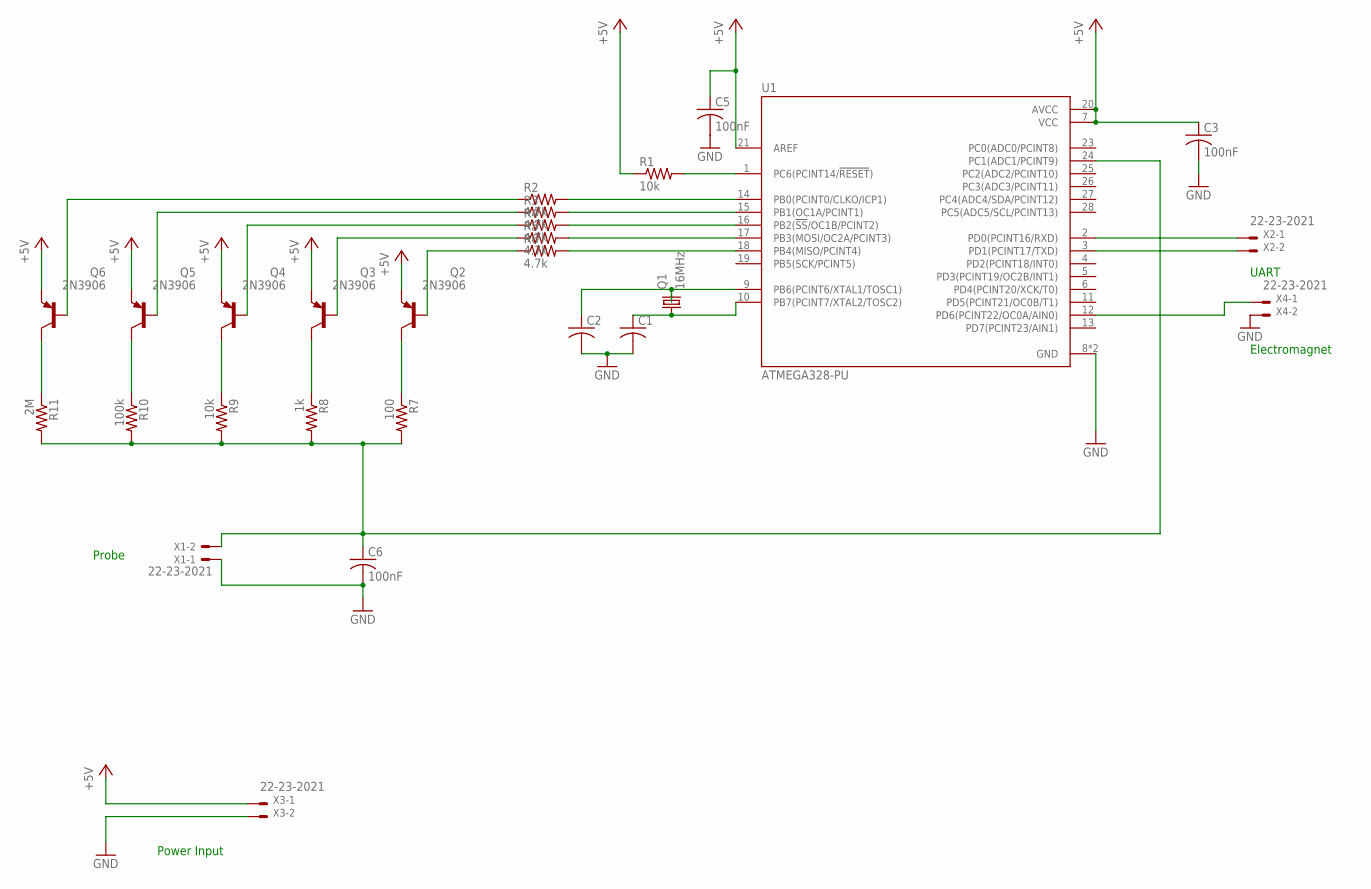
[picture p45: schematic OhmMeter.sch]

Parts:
C1, C2: C-US025-024X044; C025-024X044
C3, C5, C6: 100nF; C025-024X044
Q1: 16MHz; HC49/S
Q2, Q3, Q4, Q5, Q6: 2N3906; TO92
R1, R9: 10k; 0204/5
R2, R3, R4, R5, R6: 4.7k; 0204/5
R7: 100; 0204/5
R8: 1k; 0204/5
R10: 100k; 0204/5
R11: 2M; 0204/5
U1: ATMEGA328-PU; DIP787W46P254L3467H508Q28
X1, X2, X3, X4: 22-23-2021

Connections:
+5V: C3.1, C5.1, Q2.3 (E), Q3.3 (E), Q4.3 (E), Q5.3 (E), Q6.3 (E), R1.1, U1.7 (VCC), U1.20 (AVCC), U1.21 (AREF), X3.1
GND: C1.2, C2.2, C3.2, C5.2, C6.2, U1.8 (GND), U1.22 (GND), X1.1, X3.2, X4.2
unnamed: C2.1, Q1.2, U1.9 (PB6(PCINT6/XTAL1/TOSC1))
unnamed: C1.1, Q1.1, U1.10 (PB7(PCINT7/XTAL2/TOSC2))
unnamed: R6.2, U1.18 (PB4(MISO/PCINT4))
unnamed: R5.2, U1.17 (PB3(MOSI/OC2A/PCINT3))
unnamed: R4.2, U1.16 (PB2(!SS!/OC1B/PCINT2))
unnamed: R3.2, U1.15 (PB1(OC1A/PCINT1))
unnamed: R2.2, U1.14 (PB0(PCINT0/CLKO/ICP1))
unnamed: R1.2, U1.1 (PC6(PCINT14/!RESET!))
unnamed: Q2.2 (B), R6.1
unnamed: Q3.2 (B), R5.1
unnamed: Q4.2 (B), R4.1
unnamed: Q5.2 (B), R3.1
unnamed: Q2.1 (C), R7.1
unnamed: Q6.2 (B), R2.1
unnamed: Q3.1 (C), R8.1
unnamed: Q4.1 (C), R9.1
unnamed: Q5.1 (C), R10.1
unnamed: Q6.1 (C), R11.1
unnamed: C6.1, R7.2, R8.2, R9.2, R10.2, R11.2, U1.24 (PC1(ADC1/PCINT9)), X1.2
unnamed: U1.2 (PD0(PCINT16/RXD)), X2.1
unnamed: U1.3 (PD1(PCINT17/TXD)), X2.2
unnamed: U1.12 (PD6(PCINT22/OC0A/AIN0)), X4.1

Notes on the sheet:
Probe
UART
Power Input
Electromagnet

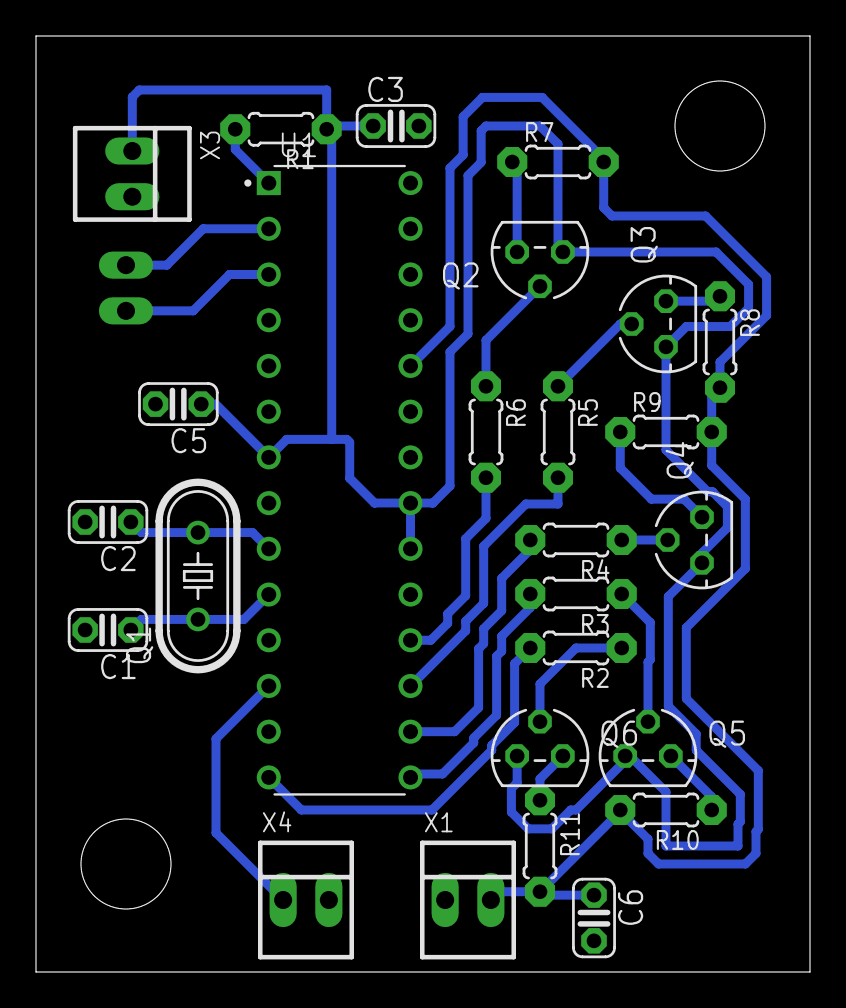
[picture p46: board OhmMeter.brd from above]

Board: 2 copper layers, 43.0 x 52.0 mm, 27 parts (1 on the bottom side), 24 nets.

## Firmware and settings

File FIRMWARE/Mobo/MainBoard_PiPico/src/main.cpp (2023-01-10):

// MAIN BOARD CODE FOR GDIP7D OHM METER ARM PROJECT
// THIS CODE IS FOR RP2040 BASED SYSTEMS (PICO,PICO W)

#include <Arduino.h>
#define _USE_MATH_DEFINES
#define BASE_HGT 67.31  // base hight 2.65"
#define SHOULDER 146.05 // shoulder-to-elbow "bone" 5.75"
#define ELBOW 276.225   // elbow-to-wrist "bone" 7.375"
#define GRIPPER 85.72   // gripper length 3.94"
// float to long
#define ftl(x) ((x) >= 0 ? (long)((x) + 0.5) : (long)((x)-0.5))
#define boxHeight 200
// This is the the tolerance for the resistor readings
#define TOLERANCE 0.1
// Define constants for arm
float sh_sq = SHOULDER * SHOULDER;
float el_sq = ELBOW * ELBOW;
float robotX = 0, robotY = 0, robotZ = 0;
//variables for conveyor belt
const int ldrPin = A0;
const int laserPin = 7;
const int dirPin = 2;
const int stepPin = 3;
const int stepsPerRevolution = 200;



// function prototypes
void runMotor();
char *getArmCode(float, float, float);
void goBackPickup();
void startAndCalibrateArm();
void moveStatusCheck();
void testValue();
void electroMagnet(int);
String listen_for_serial();
String listen_for_serial2();
// Init serial 2
UART Serial2(8, 9, NC, NC);
// Coordinates for boxes
long BoxCoordinatesXY[11][3] = {
    // Row 1
    {0, 260, 1000},  // 1k
    {0, 330, 4700},  // 4.7k
    {0, 390, 10000}, // 10k
    // Row 2
    {80, 270, 20000}, // 20k
    {80, 330, 47000}, // 47k
    {80, 390, 86000}, // 86k
    // Row 3
    {160, 270, 100000}, // 100k
    {160, 330, 180000}, // 180k
    // Row 4
    {240, 270, 470000},   // 470k
    {240, 330, 1000000}, // 1M
    {240,220,1}};        //for values not in range
// Kinematics output string
char output[256] = "";
// ========================================================================
//PROGRAM SETUP AND LOOP
void setup()
{
  Serial.begin(9600); // usb serial for debug
  Serial1.begin(9600);// UART to main board
  Serial2.begin(9600);// UART to ohm meter board
  pinMode(2, OUTPUT);// these pins are for the L298n/Electromagnet
  pinMode(3, OUTPUT);
  pinMode(4, OUTPUT);
  digitalWrite(2, LOW); 
  digitalWrite(3, HIGH);
  digitalWrite(4, LOW);
  //small delay to allow ohm meter processor to boot fully
  delay(3000);
  // send arm to startng position and calibrate
  startAndCalibrateArm();
}
void loop()
{
  // Even though the Arduino main loop is essentially the same as a while(1) loop,
  // I have noticed small bugs where certain functions such as serial will have
  // unpredictable results, such as serial printing twice on startup.
  // So I prefer to run a while(1) within the "loop", which avoids these issues
  goBackPickup();
  moveStatusCheck();
  while (1)
  {
    testValue();
    moveStatusCheck();
    electroMagnet(0);
    delay(500);
    goBackPickup();
    moveStatusCheck();
  }
}
// ========================================================================
// SERIAL FUNCTIONS:
String listen_for_serial()
{
  String message;
  if (Serial1.available() > 0)
  {
    message = Serial1.readString();

    return message;
  }
  return "";
}
String listen_for_serial2()
{
  String message;
  if (Serial2.available() > 0)
  {
    message = Serial2.readString();

    return message;
  }
  return "";
}
// ========================================================================
// ARM FUNCTIONS:
// Startup calibration function
void startAndCalibrateArm()
{

  Serial.println("#0P1425#1P1500#2P1500#3P700T2000\r");  // starting position
  Serial1.println("#0P1425#1P1500#2P1500#3P700T2000\r"); // starting position
  Serial.println("#2PO-100\r");                          // calibrate
  Serial1.println("#2PO-100\r");                         // calibrate
  Serial.println("#3PO-10\r");                          // calibrate
  Serial1.println("#3PO-10\r");                         // calibrate
  // The following delay gives time for the ohm meter board to boot to a state
  // where it is ready to receive serial commands (~2 seconds, but we do 5
  //  just to be sure)
  delay(5000);
}
// Function moves arm up back to start position, down to
// measure, then back up again
void goBackPickup()
{
  Serial.println("#0P1425#1P1500#2P1500#3P700T2000\r"); //starting pos
  Serial1.println("#0P1425#1P1500#2P1500#3P700T2000\r");
  moveStatusCheck();
  Serial.println("#0P1425#1P1243#2P1616#3P940T3000\r"); //testing pos
  Serial1.println("#0P1425#1P1243#2P1616#3P940T3000\r");
}
// checks to see if previous move is complete, if not it waits until it is
void moveStatusCheck()
{
  bool continueLoop = true;
  while (continueLoop)
  {
    Serial.println("Q\r"); // query if movement is complete
    Serial1.print("Q\r"); // query if movement is complete
    delay(50);
    String statusCheck = listen_for_serial();
    if (statusCheck == ".")
    {
      Serial.println("."); // query if movement is complete
      continueLoop = false;
      break;
    }
    else if (statusCheck == "+")
    {
      Serial.println("+"); // query if movement is complete
      continueLoop = true;
      //continue;
    }
  }
}
//Turns on/off electromagnet
void electroMagnet(int onOff)
{
  if (onOff==1){
    digitalWrite(2, LOW); 
    digitalWrite(3, HIGH);
    digitalWrite(4, HIGH);
    Serial.println("MAGNET ON");
  }
  if (onOff==0){
    digitalWrite(2, LOW); 
    digitalWrite(3, HIGH);
    digitalWrite(4, LOW);
    Serial.println("MAGNET OFF");
  }
}
// ========================================================================
// OHM METER COMMUNICATION:
void testValue()
{
  bool continueLoop = true;
  Serial.print("TEST\n");
  Serial2.print("TEST\n");
  while (continueLoop)
  {
    //delay(50);
    String checker = listen_for_serial2();

    if (checker != "")
    { 
      Serial.println(checker.toInt());
      bool valueFound = false;
      for (int i=0;i<10;i++){
        if (checker.toInt() >= (BoxCoordinatesXY[i][2] - (BoxCoordinatesXY[i][2] * TOLERANCE)) && checker.toInt() <= (BoxCoordinatesXY[i][2] + (BoxCoordinatesXY[i][2] * TOLERANCE)))
        {
          // Set valueFound to true because the value was found
          valueFound = true;
          electroMagnet(1);

          Serial.println("#0P1425#1P1500#2P1500#3P700T1000\r"); // move arm back up
          Serial1.println("#0P1425#1P1500#2P1500#3P700T1000\r");
          moveStatusCheck();
          Serial.println(getArmCode(BoxCoordinatesXY[i][0], BoxCoordinatesXY[i][1], boxHeight));
          Serial1.println(getArmCode(BoxCoordinatesXY[i][0], BoxCoordinatesXY[i][1], boxHeight));

          // Set continueLoop to false to break the loop
          continueLoop = false;
          break;
        }
      }

      // If the value was not found, skip the rest of the code in the loop and go to the next iteration
      if (!valueFound)
      { 
          electroMagnet(1);
          Serial.println("#0P1425#1P1500#2P1500#3P700T1000\r"); // move arm back up
          Serial1.println("#0P1425#1P1500#2P1500#3P700T1000\r");
          moveStatusCheck();
          Serial.println(getArmCode(BoxCoordinatesXY[10][0], BoxCoordinatesXY[10][1], boxHeight));
          Serial1.println(getArmCode(BoxCoordinatesXY[10][0], BoxCoordinatesXY[10][1], boxHeight));
        continueLoop = false;
      }
    }
  }
}
// ========================================================================
// KINEMATICS:
char *getArmCode(float x, float y, float z)
{
  float grip_angle_d = 68;
  // grip angle in radians for use in calculations
  float grip_angle_r = radians(grip_angle_d);
  // Adjustment so that the gripper hits the floor at z=0;
  z += 70;
  // Base angle and radial distance from x,y coordinates
  // float d = sqrt( x*x + y*y );    //distance from base center to x,y coordinates
  float phi = 90.00;
  float bas_angle_r = atan2(x, y);
  float L = sqrt((x * x) + (y * y));
  // L is y coordinate for the arm
  L -= cos(phi) * GRIPPER;
  y = L;
  // Grip offsets calculated based on grip angle
  float grip_off_z = (sin(grip_angle_r)) * GRIPPER;
  float grip_off_y = (cos(grip_angle_r)) * GRIPPER;
  // Wrist position
  float wrist_z = (z - grip_off_z) - BASE_HGT;
  wrist_z -= sin(phi) * GRIPPER;
  float wrist_y = y - grip_off_y;
  // Shoulder to wrist distance ( AKA sw )
  float s_w = (wrist_z * wrist_z) + (wrist_y * wrist_y);
  float s_w_sqrt = sqrt(s_w);
  // s_w angle to ground
  // float a1 = atan2( wrist_y, wrist_z );
  float a1 = atan2(wrist_z, wrist_y);
  // s_w angle to SHOULDER
  float a2 = acos(((sh_sq - el_sq) + s_w) / (2 * SHOULDER * s_w_sqrt));
  // shoulder angle
  float shl_angle_r = a1 + a2;
  float shl_angle_d = degrees(shl_angle_r);
  // elbow angle
  float elb_angle_r = acos((sh_sq + el_sq - s_w) / (2 * SHOULDER * ELBOW));
  float elb_angle_d = degrees(elb_angle_r);
  float elb_angle_dn = -(180.0 - elb_angle_d);
  // wrist angle
  float wri_angle_d = (grip_angle_d - elb_angle_dn) - shl_angle_d;
  // Servo pulses
  float bas_servopulse = 1500.0 - ((degrees(bas_angle_r)) * 11.11);
  float shl_servopulse = 1500.0 + ((shl_angle_d - 90.0) * 6.6);
  float elb_servopulse = 1500.0 - ((elb_angle_d - 90.0) * 6.6);
  float wri_servopulse = 1500 - (wri_angle_d * 11.1);
  // Set servo pulses
  // create string for output

  // Added some offsets here, not sure if they are correct, they seem to work though
  sprintf(output, "#0P%ld#1P%ld#2P%ld#3P%ldT2000\r", ftl(1500 - bas_servopulse + 500), ftl(shl_servopulse), ftl(elb_servopulse), ftl(wri_servopulse + 400));
  return output;
}


void runMotor(){
    // set direction
    digitalWrite(dirPin, LOW);
  // Begin a loop
  
  bool continueLoop = true;
  while(continueLoop){
    //rotate motor
    digitalWrite(stepPin, HIGH);
    delayMicroseconds(6000);
    digitalWrite(stepPin, LOW);
    delayMicroseconds(6000);
    int ldrStatus = analogRead(ldrPin);
    if (ldrStatus < 700)
      { 
        // keep going with the rotation
        continueLoop=true;
      }
      else
      {
        //Serial.println(" ALARM ACTIVATED ");
        // break the loop and ultimately wait for new serial command
        continueLoop = false;
      }
    }
}

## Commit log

2022-11-02 Add files via upload
    These are the Initial gripper design, the indent on the tip is for the metallic tape/strip for contacts, and the electro magnet can be mounted in the free space in between the grippers
    [Left gripper.SLDPRT, Right gripper.SLDPRT]
2022-11-09 Preliminary Gantt Chart
    Have done basic resource allocation (staffing), further allocation should be done once materials requirements and costings are defined.
2022-11-09 Clean up
    [Left gripper.SLDPRT, Right gripper.SLDPRT]
2022-11-25 PCB SCH and BRD
    [OhmMeter.brd, OhmMeter.sch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]
2022-11-28 Firmware Update
    Confirmed working hardware and code using combination of electromagnet and ohm meter on prototype gripper
    [Base v1DWGDWG.dwg, Base v1DXF.dxf, Provisional_BOM.xlsx]
2022-11-29 Add files via upload
    Updated Team Structure Flow diagram with Emre
2022-11-30 Add files via upload
    By John
    [Base v5 v1.f3d]
2022-11-30 Fusion files added
    [Base v5 v1.f3d, Provisional_BOM.xlsx, asb-09 v5.f3z]
2022-12-05 More PM stuff
    [GDIP - Concept Development.xlsx, Requirements list.xlsx, Responsibility matrix.xlsx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]
2022-12-07 Create New Project2.print
2022-12-10 Added kinematics C script and some other stuff
    Kinematics script, written for now as a C program that outputs the desired codes for the SSC-32 based on X,Y,Z positions.
    [JamesOhare_Basev5_6mmMDF_RedCut_BlackEngrave.dxf, Provisional_BOM.xlsx]
2022-12-27 Update Risk analysis - PID (Probability Impact Diagram) diagram, RAID.xlsx
    [Risk analysis - PID (Probability Impact Diagram) diagram, RAID.xlsx]
2023-01-06 Update Gripper
    [GRIPPER_FINAL.f3d, GRIPPER_FINAL.step]
2023-01-09 Exported some of the earlier gripper iterations
    [GRIPPER_OLD_V2.f3d, Gripper_old_old_V1.f3d, Left_gripper_old_old_old_V1.f3d]
2023-01-10 Update Verification and validation plan.xlsx
    [Verification and validation plan.xlsx]
2023-01-10 Firmware cleanup and other stuff
    [Mainboard.brd, Mainboard.sch]
2023-01-13 Renames Risk analysis to risk mitigation
    [Risk Mitigation plan.xlsx, Risk analysis - PID (Probability Impact Diagram) diagram, RAID.xlsx]
2023-01-13 Update Risk Mitigation plan.xlsx
    [Risk Mitigation plan.xlsx]

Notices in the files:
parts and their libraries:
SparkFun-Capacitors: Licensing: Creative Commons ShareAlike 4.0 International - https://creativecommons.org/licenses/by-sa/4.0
